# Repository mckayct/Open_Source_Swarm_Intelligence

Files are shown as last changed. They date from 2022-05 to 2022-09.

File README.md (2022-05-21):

# Open Source Swarm Intelligence
<p align="center">
Purpose: Low-Cost Open Source Swarm Capable Robots for Academic Research
</p>
<p align="center">
  
  
   
</p>

## Brief Description:

This repositiory is for the code, paper and files for swarm intelligence research I conducted at Rose-Hulman Institute of Technology under Dr. Michael Wollowski. The end goal of the research was to produce swarm capable robots for academia, that have a wide range of usability at a low-cost. The robots are originally from Kevin Thomas (user tristomietitoredeituit) on Thingiverse [SMARs](https://www.thingiverse.com/thing:2662828), and I modified a housing for them as well as combined some other features.

The final product uses a Mesh Network for communication, and is programmable in Arduino code. I have included all the CAD/STL files, as well as code for people to use. If you use these robots please feel free to share with me what you make! The best way for the swarm intelligence field to grow, is to allow more people to interact with the field.

## Table of Contents

- [Robot Overview](#robot-overview)
- [Photographs of the Robots](#photographs-of-the-robots)
- [Installation](#installation)
- [BOM](#bill-of-materials)
- [Ideas For Future](#ideas-for-future)
- [Credits](#credits)
- [License](#license)
- [Support Me](#support-me)
## Robot Overview

<p align="center">
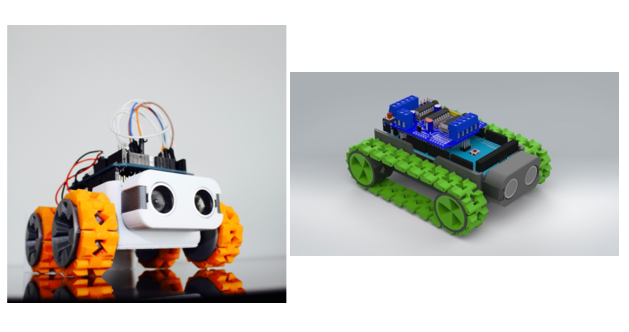
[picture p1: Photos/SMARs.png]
SMARS

</p>

The robotic platform uses a modified 3D printable open source “Screwless/Screwed Modular Assemblable Robotic System” (SMARs) originally designed by Kevin Thomas and modified by Zwald Damien. Kevin Thomas’s page details a plethora of helpful guides as well as his own outline of a teaching schedule for teaching a class with the SMARs robots visualized in Figure 2; however, this course is mainly aimed at high school level students or early undergraduate introductory courses. The SMARs platform is easily produced with a 3D printer and can be modified or expanded upon so long as the creator’s original CC BY-NC-SA 4.0 license is upheld.

<p align="center">
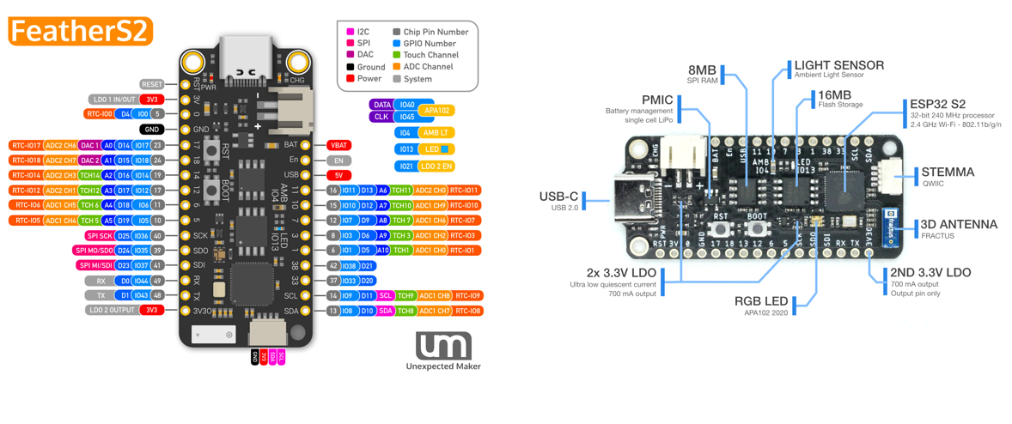
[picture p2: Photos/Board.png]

</p>

For the brain of our robot, we used the FeatherS2 by Unexpected Maker Figure(3). The ESP32-S2 microcontroller was chosen for its ability to be programmed in Arduino code, Circuit Python, or Micro Python and their built-in Wi-Fi communication. This specific ESP32-S2-based board utilizes the Adafruit Feather layout, which allows it to be compatible with Adafruit’s Wing addons. Interchanging Wing modules or stacking them allows new sensors to be added to the robot with ease via a UART connection. 

<p align="center">
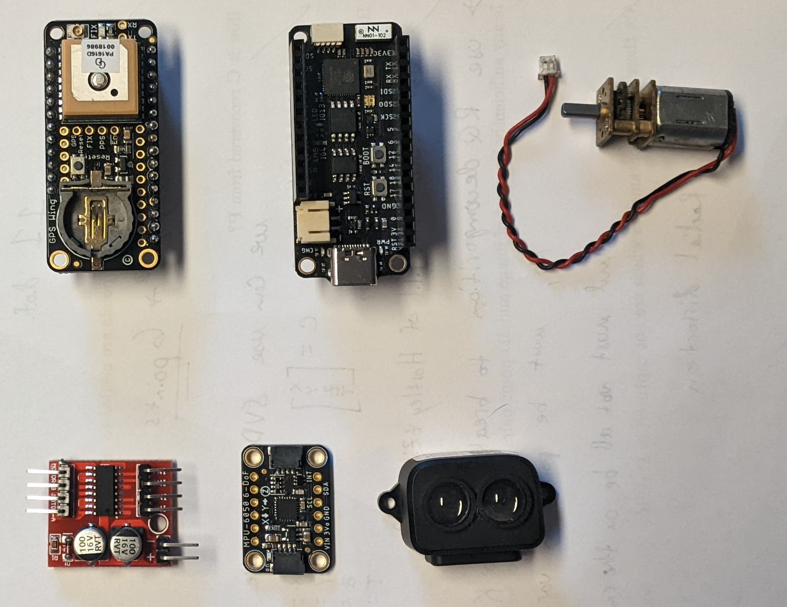
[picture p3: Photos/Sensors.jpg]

</p>
 
In addition, the board has a built-in STEMMA QT connector that allows additional sensors to be connected to the board via I2C connection protocol so long as their I2C addresses are unique. For power, a JST PH LiPo connector allows the use of a 3.7V one-cell LiPo battery which is capable of powering the robot for 6+ hours.  Mobility is provided by a mini dual-channel L298N motor driver, controlling two N20 mini-DC motors with built-in gearboxes. These low-cost motors come in many gear reduction combinations that can allow for faster acceleration or more torque depending on what the buyer is desiring.

## Photographs of the Robots

<p align="center">
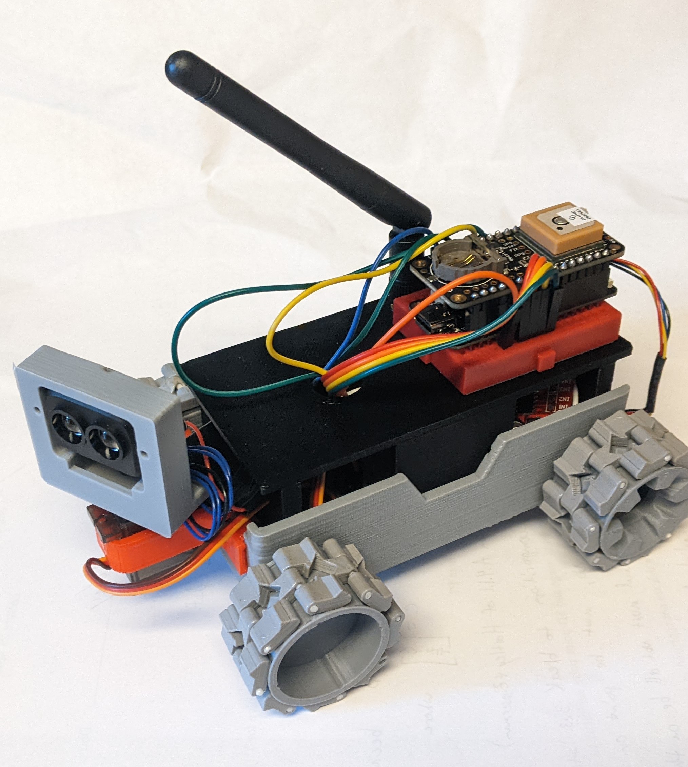
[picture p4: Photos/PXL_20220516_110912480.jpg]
ISO
  
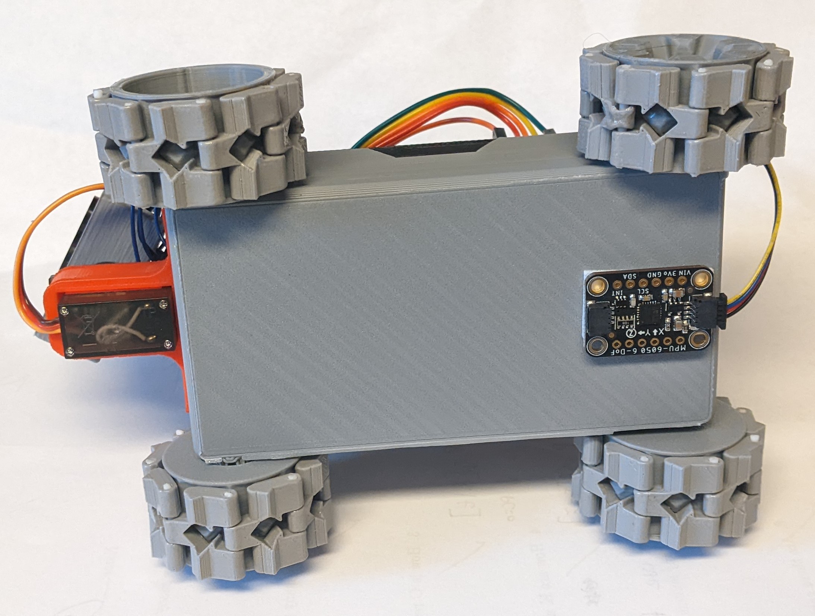
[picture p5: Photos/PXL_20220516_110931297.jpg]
BOTTOM
   
</p>

## Installation

To get the robots working you will need a computer with the Arduino IDE or Circuit Python[^first] setup. The provided code is for Arduino, but these microcontrollers are capable of being coded in either. Users are then encouraged to look through the example code provided, and modify it to their needs.

[^first]: Note at the time of writing, Circuit Python for the ESP32S2 does not support Mesh Networking, so Arduino Coding is preferred right now.

## Bill of Materials

Items are listed below. Users can use links attached or search on other websites for better deals. Sensors can also be changed depending on what the user's end goal is

| Item | Description | Quantity of Component per Robot | Price on Link[^2] | Link  |
| :----: | :---: |  :---: | :---: | :---: |
| Microcontroller | Main control board for Robot | 1 | $24.95 |[Adafruit](https://www.adafruit.com/product/4769) |
| Motor Controller | Controller for N20 Motors | 1 | $13.02 |[Amazon](https://www.amazon.com/Channel-Positive-Inversion-Adjustment-Stepper/dp/B09Y4LKV52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) |
| N20 Motors | N20 Motors with straight gearbox | 2 | $9.49 | [Ebay](https://www.ebay.com/itm/313865598591?hash=item4913d8f67f:g:mnIAAOSwYWFiAJZR)|
| MPU-6050 | 6-D.O.F. Inertial Measuring Unit | 1 | $6.95 | [Adafruit](https://www.adafruit.com/product/3886)|
| Adafruit GPS Featherwing  | Feather Sized GPS Module | 1 | $24.95 |[Adafruit](https://www.adafruit.com/product/3133) |
| TFLuna Point LiDAR | Singular Point LiDAR | 1 | $26.99 |[Amazon](https://www.amazon.com/RCmall-Single-Point-Compatible-Obstacle-Avoidance/dp/B09SZ5H21B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) |
| 9g Servo | 180 Degree Rotational Servo | 1 | $20.99 |[Amazon](https://www.amazon.com/Smraza-Helicopter-Airplane-Control-Arduino/dp/B07L2SF3R4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) |
| LiPo Battery | 2500 mAh Battery | 1 | $14.95 |[Adafruit](https://www.adafruit.com/product/328) |
| Tiny Breadboards | Minature Breadboard for cabling | 2 |  $6.49 |[Amazon](https://www.amazon.com/HiLetgo-SYB-170-Breadboard-Colorful-Plates/dp/B071KCZZ4K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) |
| Dupont Wires | For easy connection between components | 1 | $6.98 | [Amazon](https://www.amazon.com/Elegoo-EL-CP-004-Multicolored-Breadboard-arduino/dp/B01EV70C78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 )|
| 3D printed material | 3D printed components listed in CAD File | 1 | ~$10 | |

[^2]: Does not mean price per robot, nor price per component. Simply price per the link given.

## Ideas for Future

While the current robot was satisfactory for an introduction to Swarm Intelligence, I would eventually like to make them into a more final product including
* Academic Schedule for a Class Based Upon Swarm Intelligence
* Change the drive train to Tank Tread Systems (original SMARs plan)
* Creat New Algorithms for the Swarm
* Look for ways to reduce price

If you create something with this project, please reachout and share it with me!

---
## Credits

### For their Support During my Research
* Dr. Michael Wollowski
  - https://www.rose-hulman.edu/academics/faculty/wollowski-michael-wollowsk.html
  - https://www.rose-hulman.edu/~wollowsk/
* Dr. David Fisher
  - https://www.rose-hulman.edu/academics/faculty/fisher-david-fisherds.html
  - https://wordpress.rose-hulman.edu/fisherds/
* Dr. Carlotta Berry
  - https://www.rose-hulman.edu/academics/faculty/berry-carlotta-berry123.html
  - https://wordpress.rose-hulman.edu/berry123/

### For Tutorials or Foundations to my Research
* Kevin Thomas - SMARs Robot Design
  - https://www.smarsfan.com/
* Unexpected Maker
  - https://feathers2.io/
* Pat Langley
  - https://doi.org/10.1609/aimag.v42i4.15089
* Wikipedia
  - https://en.wikipedia.org/wiki/Swarm_intelligence
* Random Nerd Tutorials
  - https://randomnerdtutorials.com/esp-mesh-esp32-esp8266-painlessmesh/
* Wyss Institute
  - https://wyss.harvard.edu/technology/programmable-robot-swarms/

## License
<p align="center">
<a rel="license" href="http://creativecommons.org/licenses/by-nc-sa/4.0/">
 </a>

<br />
This work is licensed under a <a rel="license" href="http://creativecommons.org/licenses/by-nc-sa/4.0/">Creative Commons Attribution-NonCommercial-ShareAlike 4.0 International License</a>.
</p>

## Support Me
<div align="Center">
 You ABSOLUTELY DO NOT have to, but if you would like to...
 </div>
<p align="center"> 
<a href="https://www.buymeacoffee.com/mckayct" target="_blank">Buy Me A Coffee</a>
 
 </p>
<p align ="center">

</p>

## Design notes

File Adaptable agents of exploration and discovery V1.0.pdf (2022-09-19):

# Adaptable agents of exploration and discovery:

## A swarm robotics platform to facilitate research

### Advisor: Dr. Wollowski Student: Colton McKay

CSSE 435: Swarm Intelligence Dr. Wollowski
Winter/Spring 2021-22

## Abstract

Swarm Intelligence is one of the newest emerging branches of robotics research and has many opportunities for teaching at a collegiate level. As with all research, progress is expedited when more people can engage with the research. In this paper, I will showcase a simple and cheap swarm-capable robot platform. These robots can be used to allow undergraduate students or DIY experts to experiment and explore swarm intelligence. Furthermore, I will showcase an application of these robots to simulate extraterrestrial planetary navigation; an area explored by Pat Langley that I found interesting.

## Introduction

Swarm Intelligence (SI) is the study of the collective behavior of decentralized agents. From these agents, there is a form of self-organization (either natural or artificial) that can be utilized to complete some form of goal. Key aspects of SI swarms are their ability to dynamically grow and decay in population, self-autonomy (no central controlling agent), the ability for each agent within the swarm to sense its abilities and environment, and for the swarm to change goals dynamically (Wikimedia Foundation)

Following these conventions, swarm robots are generally made rather simply to allow mass production such as the Harvard Kilobots as seen in Figure 1. These robots while capable of swarm intelligence, are rather limited in their task completion capabilities. Instead, we created a low-cost robotic platform that is capable of being expanded upon over time to allow professors and students to adapt the robots to their current research goals. This modularity allows professors to utilize these robots within a classroom setting on a budget, create new course plans, or allow students to change the robots to their common goal.

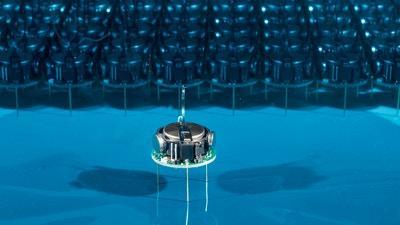
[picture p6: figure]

Figure 1: Wyss Institute at Harvard University

## The Robotic Platform

The robotic platform uses a modified 3D printable open source “Screwless/Screwed Modular Assemblable Robotic System” (SMARs) originally designed by Kevin Thomas and modified by Zwald Damien. Kevin Thomas’s page details a plethora of helpful guides as well as his own outline of a teaching schedule for teaching a class with the SMARs robots visualized in Figure 2; however, this course is mainly aimed at high school level students or early undergraduate introductory courses. The SMARs platform is easily produced with a 3D printer and can be modified or expanded upon so long as the creator’s original CC BY-NC-SA 4.0 license is upheld.

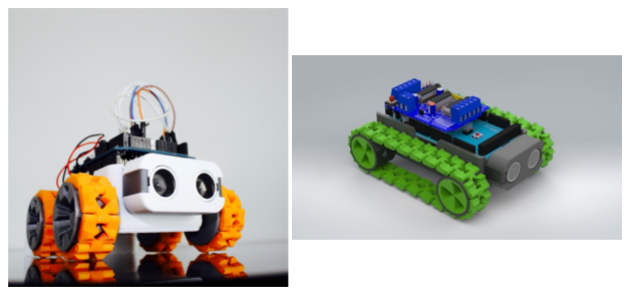
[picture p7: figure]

Figure 2: SMARS robotic platform by Kevin Thomas (left) and a remixed design by Zwald Damien (right)

For the brain of our robot, we used the FeatherS2 by Unexpected Maker Figure(3). The ESP32-S2 microcontroller was chosen for its ability to be programmed in Arduino code, Circuit Python, or Micro Python and its built-in Wi-Fi communication. This specific ESP32-S2-based board utilizes the Adafruit Feather layout, which allows it to be compatible with Adafruit’s Wing addons. Interchanging Wing modules or stacking them allows new sensors to be added to the robot with ease via a UART connection.

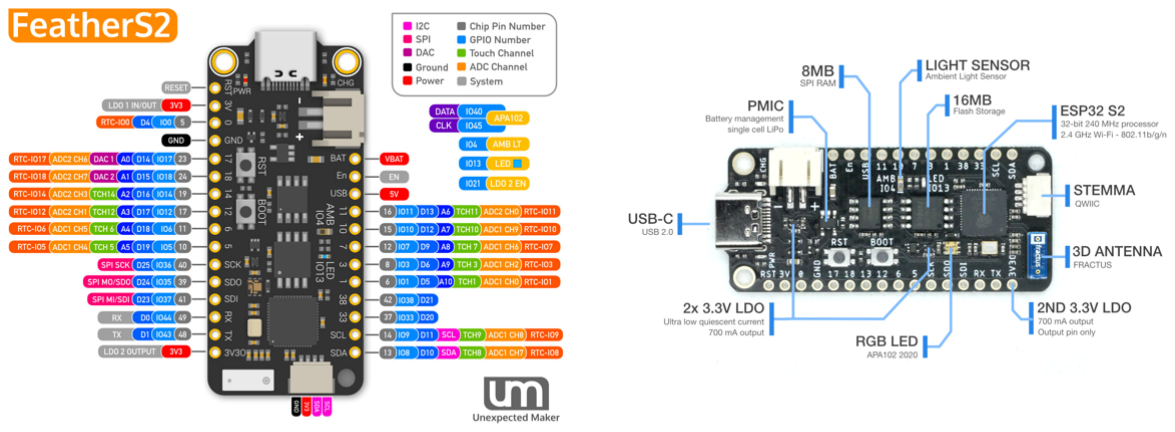
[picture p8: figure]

Figure 3: FeatherS2 features and pinout diagrams by Unexpected Maker

In addition, the board has a built-in STEMMA QT connector that allows additional sensors to be connected to the board via I2C connection protocol so long as their I2C addresses are unique. For power, a JST PH LiPo connector allows the use of a 3.7V one-cell LiPo battery which is capable of powering the robot for 6+ hours. Mobility is provided by a mini dual-channel L298N motor driver, controlling two N20 mini-DC motors with built-in gearboxes. These low-cost motors come in many gear reduction combinations that can allow for faster acceleration or more torque depending on what the buyer is desiring.

## Pat Langley’s Agents of Exploration and Discovery

Pat Langley from the Institute for Defense Analyses authored an amazing paper on the use of artificial intelligence-powered robots or “agents of exploration and discovery” to perform as modern-day pioneers that can explore new novel environments and construct maps, perform scientific experiments, and prepare for future exploration by humankind. Langley goes on further to state that these agents must be capable of autonomous behaviors, capable of variable locomotion, and able to have a variety of sensors attached to them. While the scope of our paper does not allow for professional-level robotics akin to a swarm of NASA’s JPL rovers, we can utilize the robotic platform we have made to further research

Langley suggests for these robots to be able to explore they should be able to perform Localization, Target Selection, Navigation, and Mapping. Our current system detailed above could perform a rudimentary form of Simultaneous Localization and Mapping (SLAM) via sensor fusion of the IMU, GPS, and LiDAR data. Once SLAM is performed, obstacle avoidance using LiDAR in conjunction with the map created would allow the robot to successfully navigate to areas of interest. Finally, target selection can be performed as part of the swarm’s algorithm, for example searching for a point of lowest elevation on an extraterrestrial planet as it may have extant evidence of life or exploring the highest peaks as they may contain frozen water.

While the current robots described above lack discovery capabilities, this can be expanded by adding more sensors to the system. The key points the robots should be able to perform are taxonomy formation, Descriptive law induction, and explanatory model construction. Taxonomy formation is the process of making scientific discoveries and mapping them into classes and subclasses via characteristics; therefore, providing an identification nomenclature to them. Descriptive law induction refers to taking the classes and subclasses formed within taxonomy and applying qualitative relationships or numerical equations to describe how classes and subclasses interact with each other. Once these relationships are constructed you can form the explanatory models for these discoveries. Models such as these would allow for hypotheses to be formulated, laws created, and observations documented. A picture relating all of these processes together can be seen below in Figure(2) provided by Langley.

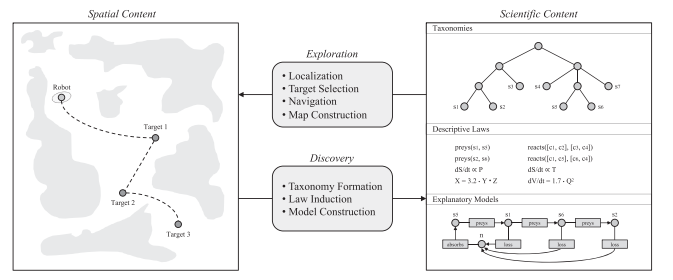
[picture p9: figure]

Figure 4: How exploration and discovery inform the complementary process of gathering spatial and scientific data

## Wollowski and McKay’s Agents of Exploration and Discovery

Using the above basis, Dr. Wollowski and I have proposed a novel example of how future research and approach agents of exploration and discovery, by harnessing the power of swarm intelligence and cheap but adaptable robotics. Our algorithm utilizes the ESP32S2’s Mesh creation tool, as well as a particle swarm optimization (PSO) approach. Our goal is for the robots to explore a foreign terrain, searching for areas of interest, in our case areas of low elevation. The data from the robots is shared by the Mesh network to allow global variable cohesion between agents in the swarm. A separate observing ESP32S2 on the network acts as our “satellite” for the agents and allows us to view the data each robot is collecting while not interfering with or controlling any of the respective agents.

## The Code

Our code written in Arduino is available on GitHub. The code uses the Painless Mesh by author Coopdis, Scotty et al. as a basis. This Mesh network is the foundation that allows our swarm to be dynamic in nature while also allowing each agent to share information globally. The network allows for each agent in the swarm to function as its own master, providing the autonomy Langley desired. A visual example of a simple network can be seen in Figure(1). Localization for the robots is provided by the onboard GPS system, which can provide accurate location data within two meters by using a universal transverse Mercator conversion from a geographic coordinate system. Our target is pre-selected, and navigation is performed by using our GPS, and LiDAR to avoid obstacles. Maps of the environment are created from LiDAR, IMU, and GPS data.

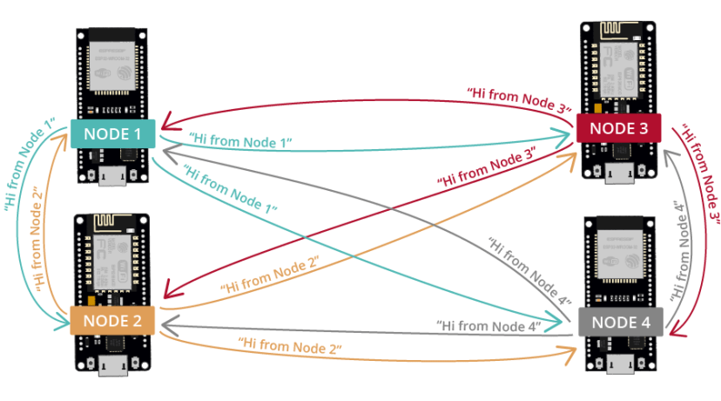
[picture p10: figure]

Figure 5: Visualization of a Mesh Network by randomnerdturotials.com

Task scheduler, an Arduino library created by Anatoli Arkhipenko is in our mesh to prevent any

one agent from controlling the network or allowing the network to fall apart. The task scheduler also schedules our robots to autonomously run functions with preset time schedules.

## The Code

The current rendition of the code is available for free at my GitHub repository, as well as plans for the robots and supporting material.

## Conclusion and Future

The following approach is easily adaptable to a university-level course on swarm intelligence. The robotics platform while cheap is very modular and can be changed to suit a novel pursuit of agents of exploration and discovery. We have included in the appendix of this paper, a rough outline of topics a typical semester-based college course could follow to teach students about swarm intelligence. Furthermore, our code, schematics, and experimentation are outlined in detail and are open source. Our experiment using a particle swarm optimization algorithm on the robotic platform was a failure as with the current code we were unable to fully implement the algorithm. In hindsight, future researchers wishing to apply the same algorithm could work to improve upon this experiment by taking the robots and building them to accommodate their own goals and procedures.

## References

1. “Introducing the feathers2!” FeatherS2, https://feathers2.io/.
2. Langley, Pat. “Agents of Exploration and Discovery.” AI Magazine, vol. 42, no. 4, 2022, pp. 72–82.,

https://doi.org/10.1609/aimag.v42i4.15089.

3. “Programmable Robot Swarms.” Wyss Institute, 28 May 2021,

https://wyss.harvard.edu/technology/programmable-robot-swarms/.

4. Strobistar, et al. “ESP-Mesh with ESP32 and ESP8266: Getting Started.” Random Nerd Tutorials, 23 Nov.

2020, https://randomnerdtutorials.com/esp-mesh-esp32-esp8266-painlessmesh/.

5. “Swarm Intelligence.” Wikipedia, Wikimedia Foundation, 26 Apr. 2022,

https://en.wikipedia.org/wiki/Swarm_intelligence.

6. “Welcome to SMARS Fan.” RSS, https://www.smarsfan.com/.

## Appendix

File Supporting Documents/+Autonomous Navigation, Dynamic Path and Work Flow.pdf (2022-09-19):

ABSTRACT

Kennedy Space Center has teamed up with the Biological Computation Lab at the University of New Mexico to create a swarm of small, low-cost, autonomous robots, called Swarmies, to be used as a ground-based research platform for in-situ resource utilization missions. The behavior of the robot swarm mimics the central-place foraging strategy of ants to find and collect resources in an unknown environment and return those resources to a central site. The swarm has no prior knowledge of the environment, uses trails as a simple indirect communication strategy, and evolves a set of behavioral parameters using a genetic algorithm. The evolution of the parameters allows the swarm to maximize collection rates while adapting to new environmental conditions and to various unknown resource distributions. The goal of this research is to add new in-situ resource utilization related behaviors to the genetic algorithm and to increase the autonomy of the system.

ANTICIPATED BENEFITS
To NASA funded missions:
This research area provides several possible benefits to NASA’s Science Technology Mission Directorate (STMD) Game Changing Development (GCD) Human Robotic System (HRS) projects such as Regolith Advanced Surface Systems Operations Robot (RASSOR) 2 which is under development at KSC’s Swamp Works. Off-planet applications of such a system include water-ice detection and mining, terrain mapping and habitat construction in advance of human explorers. The confirmation of the viable concept of operations along with the proof of concepts for autonomous navigation, path planning, and power management could improve performance and reliability of in-situ robotic mining agents such as RASSOR2. The

Two Swarmie robots are shown here searching for resources, or bar codes. NASA photo.

Table of Contents
Abstract
Anticipated Benefits
Technology Maturity
Management Team
Technology Areas
Detailed Description
U.S. Locations Working on this Project
Image Gallery
Details for Technology 1
Details for Technology 2
Details for Technology 3

Completed Project (2014 - 2015)

## Autonomous Navigation, Dynamic Path and Work Flow Planning in Multi-Agent Robotic Swarms Project

Center Innovation Fund: KSC CIF Program | Space Technology Mission
Directorate (STMD)

For more information visit techport.nasa.gov

Some NASA technology projects are smaller (for example SBIR/STTR, NIAC and Center Innovation Fund), and will have less content than other, larger projects. Newly created projects
may not yet have detailed project information. | Printed 7/24/2015

Page 1

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
10 development environment, including the simulation verification environment, along with the low cost robotic platforms reduce the cost of design and development of software for these types of applications.
To NASA unfunded & planned missions:
This research provides potential benefit to any unfunded & planned NASA missions such as OxMiner or an Asteroid Retrieval Mission engaged in in-situ resource mining. Off-planet applications of such a system include water-ice detection and mining, terrain mapping and habitat construction in advance of human explorers. The confirmation of the viable concept of operations along with the proof of concepts for the autonomous navigation, path planning, and power management improves performance and reliability of in-situ robotic mining agents.The development environment, including the simulation verification environment, along with the low cost robotic platforms reduce the cost of design and development of software for these types of applications.
To other government agencies:
This research provides potential benefit to other government agencies such as the Department of Defense (DOD) or Defense Advanced Research Projects Agency (DARPA) engaged in in-situ resource location and operations. Terrestrial applications include search-and-rescue, hazardous waste cleanup, land mine removal and infrastructure inspection and repair. The approach used in the software could also be adapted to search the Internet or to search large unknown data sets. The confirmation of the viable concept of operations along with the proof of concepts for the autonomous navigation, path planning, and power management improves performance and reliability of in-situ robotic operations. The development environment, including the simulation verification environment, along with the
Lowest: 2 | | Highest: 3
1 | 2 | | 3 | 4 | 5 | 6 | 7 | 8 | 9
Applied Research | | | | Develop- ment | | | Demo & Test

Technology Maturity

Management Team
Program Executive:
John Falker

Program Manager:
Nancy Zeitlin

Project Manager:
Kurt Leucht

Principal Investigator:
Kurt Leucht

Co-Investigator:
Karl Stolleis

Technology Areas
Robotics, Tele-Robotics &
Autonomous Systems (TA 4)

## Autonomous Navigation, Dynamic Path and Work Flow Planning in Multi-Agent Robotic Swarms Project

Center Innovation Fund: KSC CIF Program | Space Technology Mission
Directorate (STMD)

For more information visit techport.nasa.gov

Some NASA technology projects are smaller (for example SBIR/STTR, NIAC and Center

Page 2 low cost robotic platforms reduce the cost of design and development of software for these types of applications.
To the commercial space industry:
This research provides potential benefit to the commercial space industry commercial asteroid mining ventures which are proposed by Planetary Resources, Inc., Deep Space Industries, Inc. Moon Express, Astrobotics, or any entity engaged in in-situ resource location and operations. Off-planet applications of such a system include water-ice detection and mining, terrain mapping and habitat construction in advance of human explorers. The confirmation of the viable concept of operations along with the proof of concepts for the autonomous navigation, path planning, and power management improves performance and reliability of in-situ robotic operations. The development environment, including the simulation verification environment, along with the low cost robotic platforms reduce the cost of design and development of software for these types of applications.
To the nation:
Terrestrial applications include search-and-rescue, hazardous waste cleanup, land mine removal and infrastructure inspection and repair. The approach used in the software could also be adapted to search the Internet or to search large unknown data sets. The development environment, including the simulation verification environment, along with the low cost robotic platforms reduce the cost of design and development of software for these types of applications.These technologies could make these terrestrial operations safer and more efficient via swarming robotic means.

DETAILED DESCRIPTION

As humans push further beyond the grasp of earth, robotic missions in advance of human missions will play an increasingly important role. These robotic systems will find and collect valuable resources as part of an in-situ resource utilization strategy. They will need to be highly autonomous while maintaining high task performance levels.
Kennedy Space Center has teamed up with the Biological Computation Lab at the University of New Mexico to create a swarm of small, low-cost, autonomous robots, called Swarmies, to be used as a ground-based research platform for in-situ resource utilization missions. The behavior of the robot swarm mimics the central-place foraging strategy of ants to find and collect resources in an unknown environment and return those resources to a central site. The swarm has no prior

## Autonomous Navigation, Dynamic Path and Work Flow Planning in Multi-Agent Robotic Swarms Project

Center Innovation Fund: KSC CIF Program | Space Technology Mission
Directorate (STMD)

For more information visit techport.nasa.gov

Some NASA technology projects are smaller (for example SBIR/STTR, NIAC and Center

Page 3 knowledge of the environment, uses trails as a simple indirect communication strategy, and evolves a set of behavioral parameters using a genetic algorithm. The evolution of the parameters allows the swarm to maximize collection rates while adapting to new environmental conditions and to various unknown resource distributions.
The goal of this research is to add new in-situ resource utilization related behaviors to the genetic algorithm and to increase the autonomy of the system. Digital trails that are based on ant pheromone trails provide simple communication of resource locations between robots but they also provide some assistance with obstacle avoidance and navigation. Two newly evolved genetic algorithm parameters allow the robots to recharge their batteries autonomously without loss of robots due to insufficient charge. The genetic algorithm is able to optimize collection rates while also dealing with relatively high system error due to inexpensive and sub-optimal sensors onboard the robots. The distributed nature of the robotic swarm prevents a single point of failure and allows the system to operate even with the loss of one or more robots.
Off-planet applications of such a system include water-ice detection and mining, terrain mapping and habitat construction in advance of human explorers. Terrestrial applications include searchand-rescue, hazardous waste cleanup, land mine removal and infrastructure inspection and repair. The approach used in the software could also be adapted to search the Internet or to search large unknown data sets.
This project has helped demonstrate that in an obstacle laden environment, trails used as a simple indirect communication strategy can allow a swarm of small, low-cost robots to collect resources in an optimal manner when coupled with a genetic algorithm to evolve behaviors. This project has also helped demonstrate that an autonomous robot swarm can evolve battery charging behavior using a genetic algorithm to minimize or eliminate dead robots due to insufficient charge.
The project has been successful in meeting the original goals in simulated field trials and also in real robots. The genetic algorithm is able to evolve optimal behaviors allowing for efficient resource collection while coping with various obstacle arrangements and resource distributions. The genetic algorithm is also able to maintain a high level of fitness while incorporating autonomous recharging of the robots. It has also been demonstrated that this system is error tolerant, adaptable to different robot types, and is scalable in both environment size and numbers of robots.
All of these robot behaviors are performed in real-time with a small, low-cost onboard computer and small memory footprint. The robot platform is constructed using commercial off-the-shelf parts and

## Autonomous Navigation, Dynamic Path and Work Flow Planning in Multi-Agent Robotic Swarms Project

Center Innovation Fund: KSC CIF Program | Space Technology Mission
Directorate (STMD)

For more information visit techport.nasa.gov

Some NASA technology projects are smaller (for example SBIR/STTR, NIAC and Center

Page 4

3D printed parts with a total cost of less than $1,500 per robot.
A secondary goal of this project was to extend the genetic algorithm to other new and commercially available robot platforms. Another secondary goal was to use open source software frameworks to help reduce barriers and allow future researchers to more easily utilize genetic algorithms for behavior evolution in a swarm of robots. The project has been successful in meeting both of these secondary goals.
This autonomous mobile robot system is a foundation for future research into the suitability of robot swarms and evolutionary algorithms for in-situ resource utilization missions. The low-cost of this type of system removes one of the barriers typically associated with swarm operation and research. Such research should prove valuable as humans explore harsh, remote, or inaccessible locations where teleoperation is required.

## Autonomous Navigation, Dynamic Path and Work Flow Planning in Multi-Agent Robotic Swarms Project

Center Innovation Fund: KSC CIF Program | Space Technology Mission
Directorate (STMD)

For more information visit techport.nasa.gov

Some NASA technology projects are smaller (for example SBIR/STTR, NIAC and Center

Page 5

## Autonomous Navigation, Dynamic Path and Work Flow Planning in Multi-Agent Robotic Swarms Project

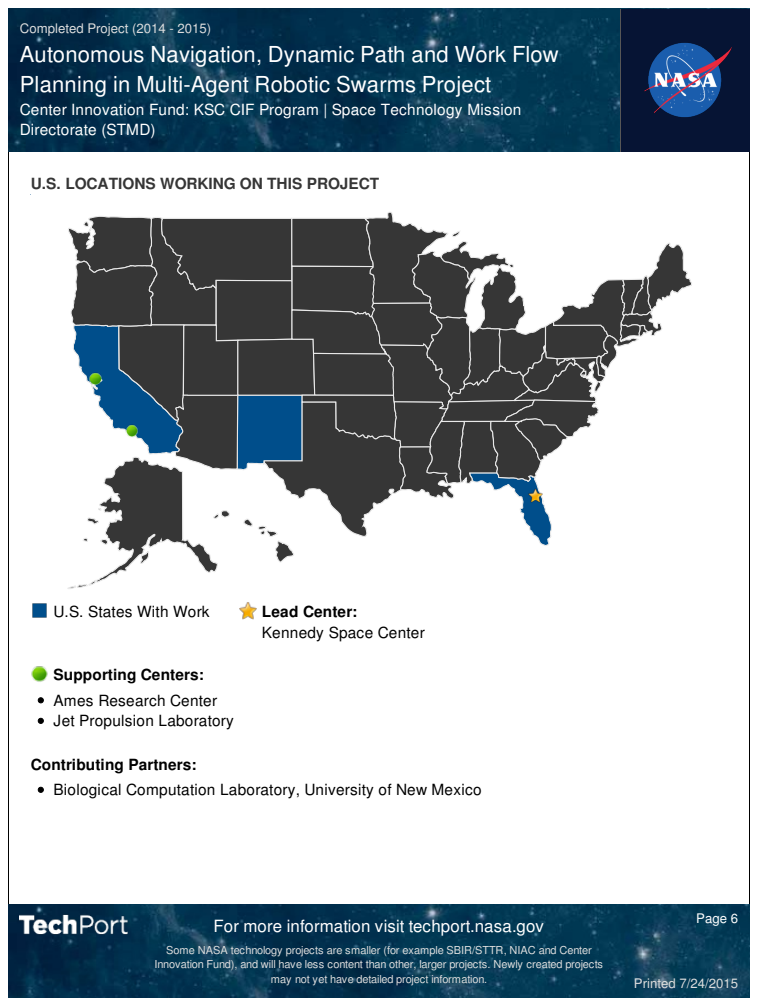
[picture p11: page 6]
U.S. States With Work; Lead Center:; Page 6

Center Innovation Fund: KSC CIF Program | Space Technology Mission
Directorate (STMD)

U.S. LOCATIONS WORKING ON THIS PROJECT

Kennedy Space Center

Supporting Centers:
Ames Research Center
Jet Propulsion Laboratory

Contributing Partners:
Biological Computation Laboratory, University of New Mexico

For more information visit techport.nasa.gov

Some NASA technology projects are smaller (for example SBIR/STTR, NIAC and Center

PROJECT LIBRARY
News Stories
Discovery News: Swarmie Space Robots Forage Like Ants (http://news.discovery.com/tech/robotics/swarmie-space-robots-forage-like-ants-140821.htm)
Engadget: NASA's Swarmies are a squad of smaller, less intelligent rovers (http://www.engadget.com/2014/08/27/nasa-swarmies/)
Fast Company: These Robots Will Mine Outer Space For Water And Minerals (http://www.fastcoexist.com/3034904/these-robots-will-mine-outer-space-for-water-andminerals)
IEEE Spectrum: NASA Training Swarmie Robots for Space Mining (http://spectrum.ieee.org/automaton/robotics/military-robots/nasa-training-swarmie-robotsfor-space-mining)
NASA Kennedy YouTube video: Inside KSC! Feb 27, 2015 (https://www.youtube.com/watch?v=mYlBabMIesE)
NASA Kennedy YouTube video: Swarmies Work Through Field Tests (https://www.youtube.com/watch?v=kjSD6DWk0OM)
NASA Website: Meet The Swarmies - Robotics Answer to Bugs (http://www.nasa.gov/content/meet-the-swarmies-robotics-answer-to-bugs/) NASA Website: Swarmies Shuffle Through Field Tests (http://www.nasa.gov/content/swarmies-shuffle-through-field-tests/)
SPACE.com: NASA's Robot Army of Swarmies Could Explore Other Planets (http://www.space.com/26935-nasa-robot-swarmies-army-space-exploration.html) Spaceport Magazine (cover story): Robots Take World by Swarm (http://issuu.com/spaceportmagazine/docs/september_spm)
Spaceport Magazine: Engineers seek more efficient search from Swarmies Continued on following page.

## Autonomous Navigation, Dynamic Path and Work Flow Planning in Multi-Agent Robotic Swarms Project

Center Innovation Fund: KSC CIF Program | Space Technology Mission
Directorate (STMD)

For more information visit techport.nasa.gov

Some NASA technology projects are smaller (for example SBIR/STTR, NIAC and Center

Page 7

News Stories (cont.)
(http://issuu.com/spaceportmagazine/docs/spaceport_magazine_____march_2015) WOFL FOX 35 Orlando (video segment): NASA programming robots to act like ants (http://www.myfoxorlando.com/story/26427492/nasa-programming-robots-to-act-like-ants)

This image shows a computer simulation of a swarm of robots searching for resources, or bar codes, among a field of obstacles. The inlay shows a map containing obstacles in white and found resources in black.

This image shows a swarm of four robots searching for resources, or bar codes, in a NASA parking lot.

IMAGE GALLERY

DETAILS FOR TECHNOLOGY 1

Technology Title
Autonomy
Technology Description
This technology is categorized as complex electronics software for ground support or mission operations
see detailed description
Capabilities Provided
see detailed description

Technology Areas
Other Technology Areas:
Robotics, Tele-Robotics &
Autonomous Systems (TA 4)

## Autonomous Navigation, Dynamic Path and Work Flow Planning in Multi-Agent Robotic Swarms Project

Center Innovation Fund: KSC CIF Program | Space Technology Mission
Directorate (STMD)

For more information visit techport.nasa.gov

Some NASA technology projects are smaller (for example SBIR/STTR, NIAC and Center

Page 8

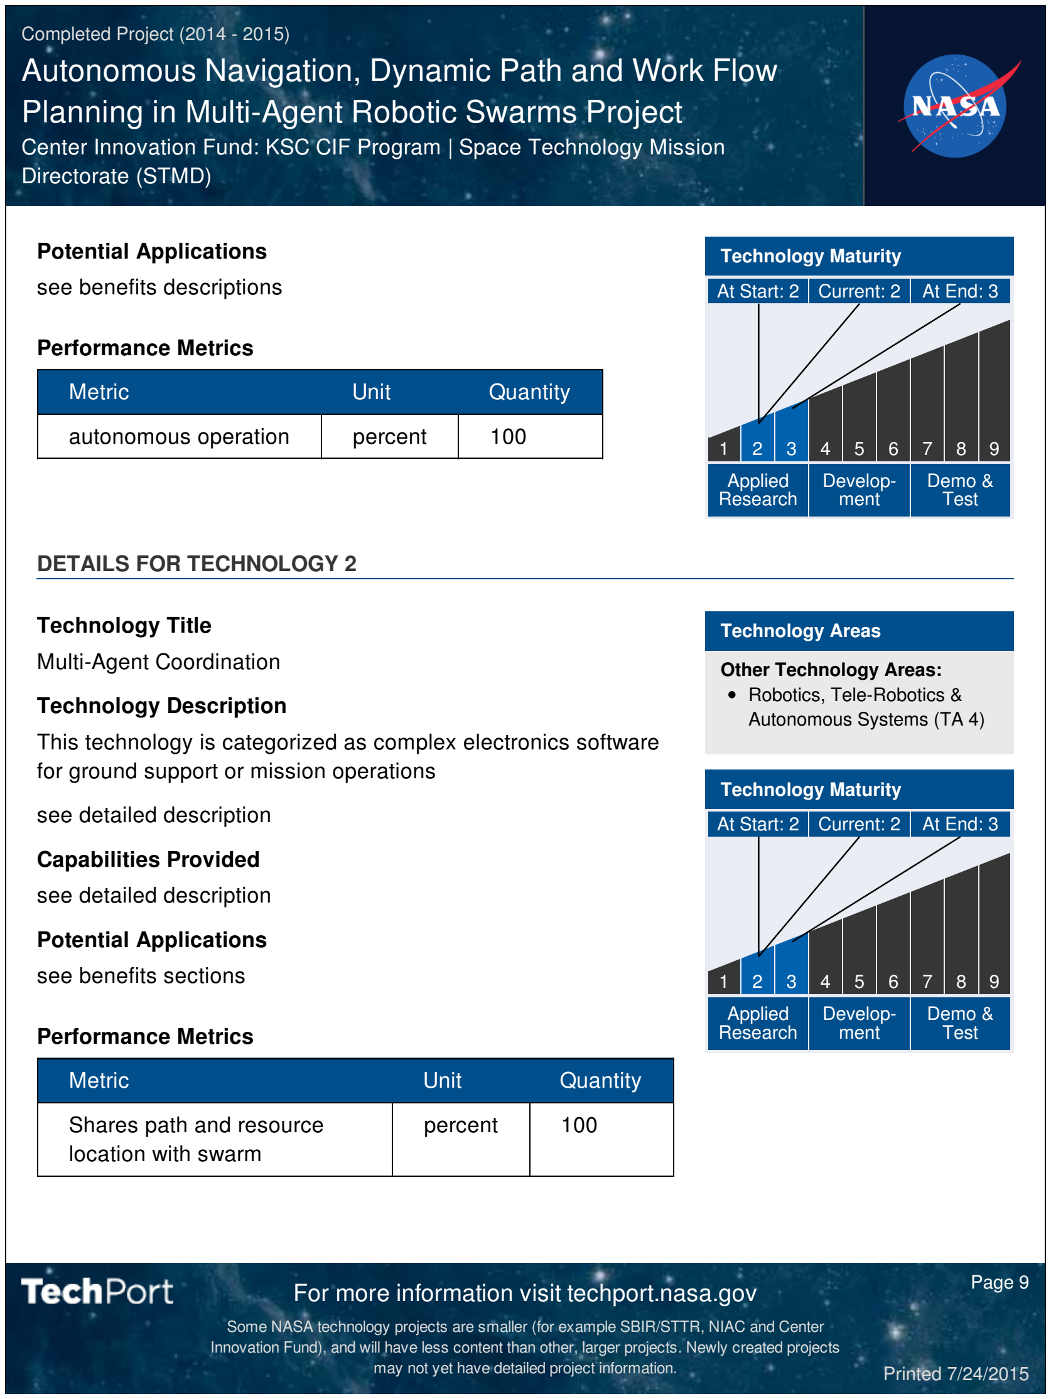
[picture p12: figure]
Potential Applications see benefits descriptions; Performance Metrics; Metric; Unit; Quantity; autonomous operation; percent; At Start: 2; Current: 2; At End: 3; Applied Research; Develop- ment; Demo & Test; Technology Maturity; DETAILS FOR TECHNOLOGY 2; Technology Title Multi-Agent Coordination; Technology Description; see detailed description; Capabilities Provided see detailed description; Potential Applications see benefits sections; Shares path and resource location with swarm; Technology Areas; Other Technology Areas: Robotics, Tele-Robotics & Autonomous Systems (TA 4)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

This technology is categorized as complex electronics software for ground support or mission operations

## Autonomous Navigation, Dynamic Path and Work Flow Planning in Multi-Agent Robotic Swarms Project

Center Innovation Fund: KSC CIF Program | Space Technology Mission

Some NASA technology projects are smaller (for example SBIR/STTR, NIAC and Center

DETAILS FOR TECHNOLOGY 3

Technology Title
Path and Motion Planning with Uncertainty
Technology Description
This technology is categorized as complex electronics software for ground support or mission operations
see details description
Capabilities Provided
see details description
Potential Applications
see benefits section

Performance Metrics
Metric | Unit | Quantity
navigates successfully to resource | percent | 100
At Start: 2 | Current: 2 | At End: 3

Applied
Research

Develop- ment

Demo &
Test

Technology Areas
Other Technology Areas:
Robotics, Tele-Robotics &
Autonomous Systems (TA 4)

Technology Maturity

## Autonomous Navigation, Dynamic Path and Work Flow Planning in Multi-Agent Robotic Swarms Project

Center Innovation Fund: KSC CIF Program | Space Technology Mission
Directorate (STMD)
1 | 2 | 3 | 4 | 5 | 6 | 7 | 8 | 9

For more information visit techport.nasa.gov

Some NASA technology projects are smaller (for example SBIR/STTR, NIAC and Center

Page 10

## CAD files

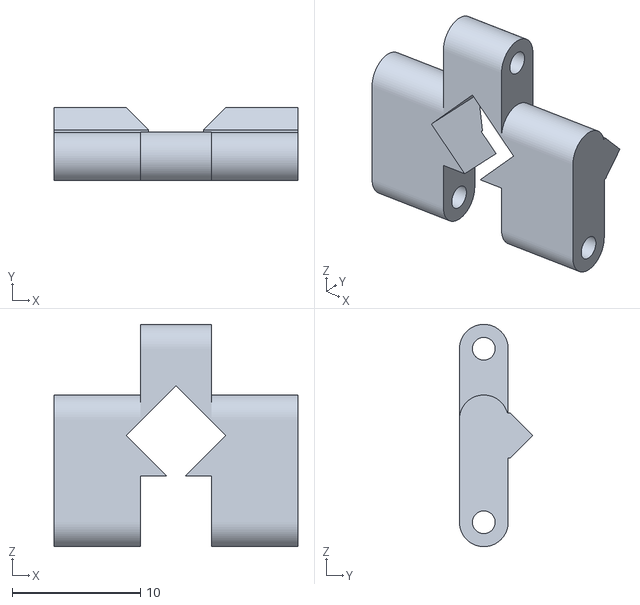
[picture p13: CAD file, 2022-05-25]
CAD/SMARS-Chain.STL
19.0 x 5.70 x 17.3

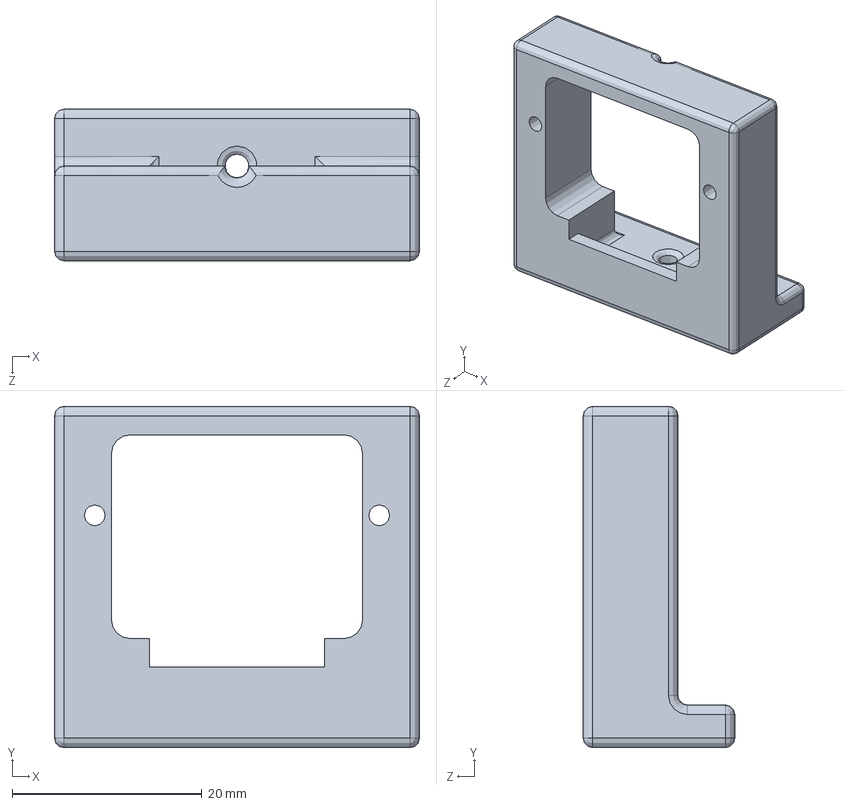
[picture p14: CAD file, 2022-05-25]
CAD/LiDAR Holder.SLDPRT
38.5 x 36.0 x 16.0 mm

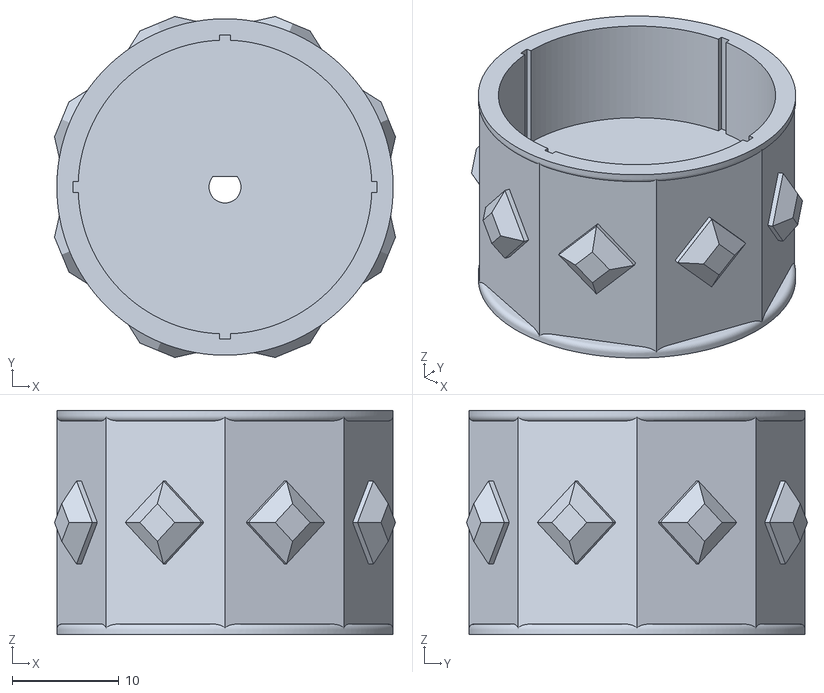
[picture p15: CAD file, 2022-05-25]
CAD/SMARS-Drive-Wheel.STL
31.9 x 31.9 x 21.0

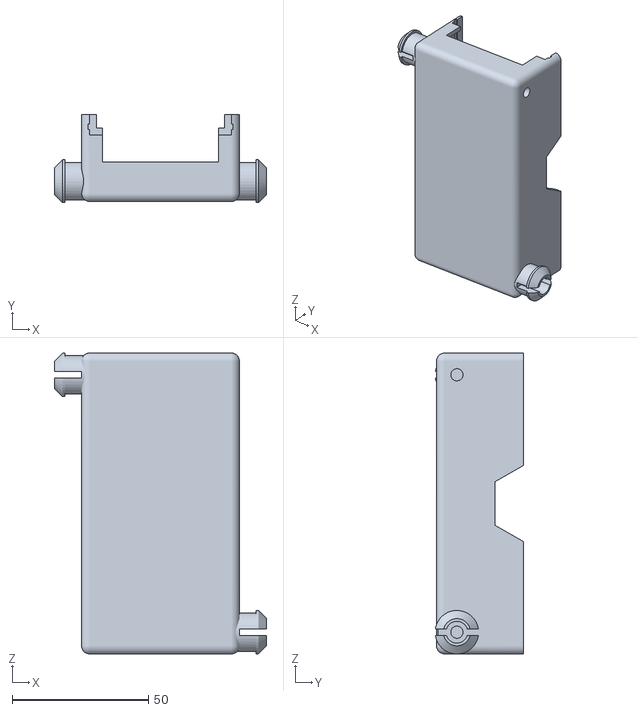
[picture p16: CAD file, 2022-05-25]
CAD/SMARS-Chassis-L-No-Middle-Partition.stl
78.0 x 32.4 x 110.5

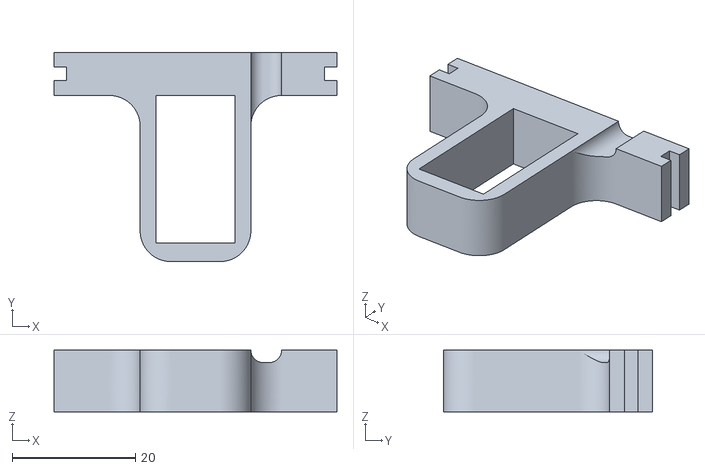
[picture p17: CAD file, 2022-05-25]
CAD/Servo-Holder.stl
46.0 x 34.0 x 10.0

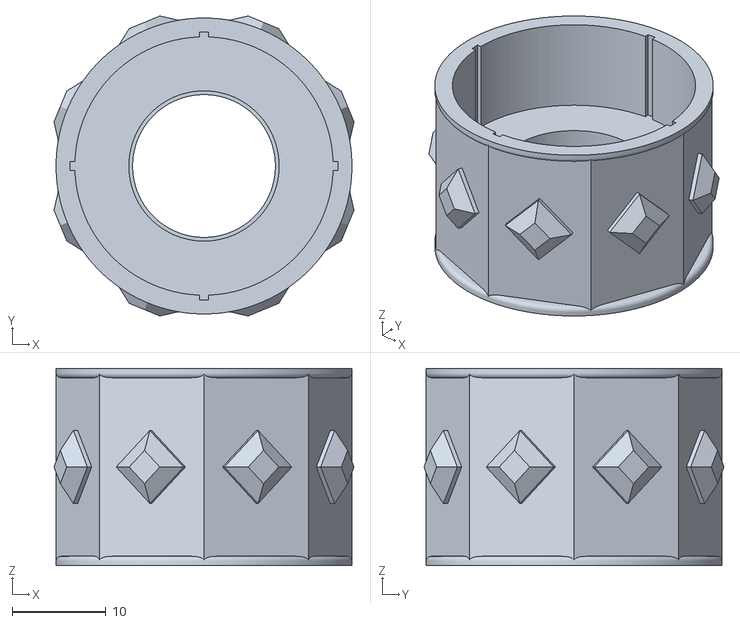
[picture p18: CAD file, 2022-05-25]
CAD/SMARS-Passive-Wheel.STL
31.9 x 31.9 x 21.0

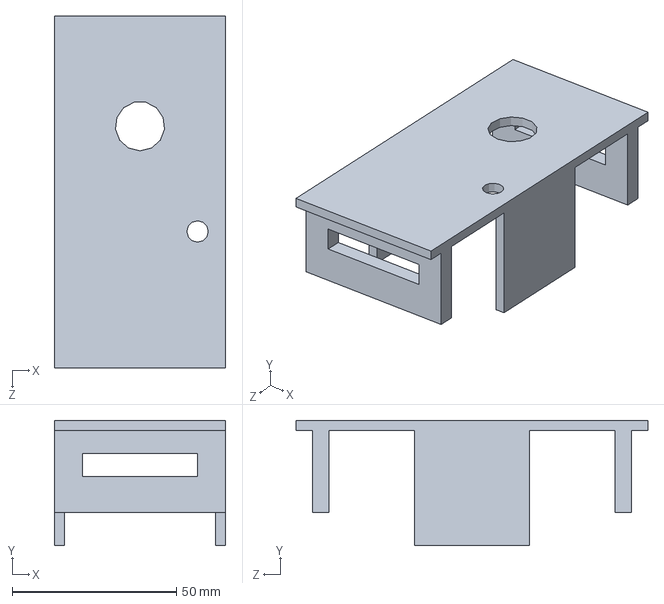
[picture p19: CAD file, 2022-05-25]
CAD/Faceplate.SLDPRT
52.0 x 38.0 x 107.0 mm

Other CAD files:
CAD/Faceplate.STL
CAD/LiDAR Holder.STL

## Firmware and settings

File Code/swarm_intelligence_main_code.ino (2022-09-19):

 /* Swarm Intelligence Code
  Rose-Hulman Institute of Technology
  Winter-Spring 2021-22

  By: Colton McKay
      school email: mckayct@rose-hulman.edu
      personal email: wcsm1999@yahoo.com

  Advisor: Dr. Wollowski

  Description:
  This code is the main driving code for my swarm robots (for more information on them see README).
  The code uses a painlessMesh Library to form a WIFI network using ESP-MESH protocals, this allows for dynamic network decay and growth
  The code also includes our algorithm for what the Robots must accomplish as well as some defined movement functions.
  My coding style is not "Rose-Hulman" standard, but I organize it into logical chunks for easier understanding. If future students need any help
  or would like to understand my work flow/process feel free to reach out to me via contact info above.

*/

// Import of Libraries
#include <basicMPU6050.h> 
#include <Adafruit_GPS.h>
#include <Adafruit_Sensor.h>
#include <Wire.h>
#include <Arduino.h>     // every sketch needs this
#include <TFLI2C.h>      // TFLuna-I2C Library v.0.2.0
#include <L298NX2.h>
#include "painlessMesh.h" //Used for making the WIFI Mesh Network


//**********************************************************
// #Defines go here

#define GPSSerial Serial1 // Define GPS Serial Connection
#define   MESH_PREFIX     "swarmIntelligence" // WIFI Network Name
#define   MESH_PASSWORD   "swarmsRCool" // WIFI Network Password
#define   MESH_PORT       5555 // TCP Port Network runs on, 5555 is default
#define GPSECHO false //Set to true to print Raw GPS Data to Serial. For Debugging only!
//  Pin definition
//Motor A Pins
const unsigned int EN_A = 3;
const unsigned int IN1_A = 5;
const unsigned int IN2_A = 6;
//Motor B Pins
const unsigned int IN1_B = 7;
const unsigned int IN2_B = 8;
const unsigned int EN_B = 9;
//Constants for Measuring Motion Time
unsigned long startMillis;  //some global variables available anywhere in the program
unsigned long currentMillis;
const unsigned long period = 1000;  //the value is a number of milliseconds (1 second), scale as needed
const unsigned long timeConstInches = 10; // Constant variable in milliseconds that translate to roughly 1 inch of motion
const unsigned long timeConstDegree = 10; // Constant variable in milliseconds that translate to roughly 1deg of rotation motion
//Constants for LIDAR
int16_t tfDist;    // distance in inches (sensor reads in cm, I have converted)
int16_t  tfAddr = TFL_DEF_ADR;  // use this default I2C address or
//Servo for LIDAR
const int servoPin = 17;
int dutyCycle = 0;
const int PWMFreq = 50;                                //50hz
const int PWMChannel = 0;
const int PWMResolution = 12;                       //12 bits 0-4095

//***********************************************************************
// Declare Class objects Here

Scheduler userScheduler; // to control your personal task
painlessMesh  mesh; //Create a mesh
L298NX2 motors(EN_A, IN1_A, IN2_A, EN_B, IN1_B, IN2_B);// Initialize both motors
Adafruit_GPS GPS(&GPSSerial);//Define GPS Object
TFLI2C tflI2C;
basicMPU6050<> imu;


//**********************************************************************
// Declare Global Variables Here

void sendMessage() ; // Prototype so PlatformIO doesn't complain
//void updateLocalVariables();
//void updateGlobalVariables();
//void algorithm();
//void readData();
//void obstacleAvoidance();
////void gatherData();
//void randomStart();
//void movements();
//**********************************************************************
// Declare Tasks for Task Manager Here
//(WHEN, HOW OFTEN, TASK)
Task taskSendMessage( TASK_SECOND*1 ,1000, &sendMessage ); // Used to Ping to Network, Data

//Task taskRandomStart( -1 ,0, &randomStart);
//
//Task tastkUpdateGlobalVariables(-1, 0, &updateGlobalVariables );//Used to check and update Global Variables
//
//Task taskUpdateLocalVariables(-1, 0, &updateLocalVariables  );// Used to check and update Local Variables
//
//Task taskReadData(-1,TASK_FOREVER, &readData );// Used to check and update Local Variables
//
//Task taskAlgorithm(-1, 0, &algorithm );
//
//Task taskGatherData(TASK_SECOND*1 ,1000, &gatherData );
//
//Task taskobstacleAvoidance(-1, 0, &obstacleAvoidance );
//
//Task taskMovement(-1, 0, &movements );

  bool firstTime = false;


  //Global Variables
  float g_best[3];

  //Local Variables
  float l_best[3];
  float l_current[3];
  float movement[2];
  
  //Setup Arrays
  float gps[5];
  float imu_data[7];
  float lidar_sweep[100];
  float temp_sweep_min[1];

  //Parameters
  float dist_threshold = 100;





//**********************************************************************
// Primary Functions - SETUP (runs 1 time) and LOOP (runs Infinite times)
void setup() {
  Serial.begin(115200);
//  startMillis = millis();
  //mesh.setDebugMsgTypes( ERROR | MESH_STATUS | CONNECTION | SYNC | COMMUNICATION | GENERAL | MSG_TYPES | REMOTE ); // all types on
  //MESH FUNCTION
  mesh.setDebugMsgTypes( ERROR | STARTUP );  // set before init() so that you can see startup messages
  mesh.init( MESH_PREFIX, MESH_PASSWORD, &userScheduler, MESH_PORT );
  mesh.onReceive(&receivedCallback);
  mesh.onNewConnection(&newConnectionCallback);
  mesh.onChangedConnections(&changedConnectionCallback);
  mesh.onNodeTimeAdjusted(&nodeTimeAdjustedCallback);

  //GPS
//  GPS.begin(9600);
//  GPS.sendCommand(PMTK_SET_NMEA_OUTPUT_RMCGGA);  // uncomment this line to turn on RMC (recommended minimum) and GGA (fix data) including altitude
//  GPS.sendCommand(PMTK_SET_NMEA_UPDATE_1HZ); // 1 Hz update rate
  // For the parsing code to work nicely and have time to sort thru the data, and
  // print it out we don't suggest using anything higher than 1 Hz

  //MPU
  // Set registers - Always required
//  imu.setup();
  // Initial calibration of gyro
//  imu.setBias();

  //Servos
//  Wire.begin();
  
  //TASK SCHEDULER
  userScheduler.addTask( taskSendMessage );
//  userScheduler.addTask(taskGatherData);
//  taskGatherData.enable();
  taskSendMessage.enable();

//  ledcSetup(PWMChannel, PWMFreq, PWMResolution);
//  ledcAttachPin(servoPin, PWMChannel);
//  ledcWrite(PWMChannel, dutyCycle);
//  
  
}

void loop() {
  mesh.update();   // it will run the user scheduler as well
}

//____________________________________________________________________________________________________________________________________________________________________________
//**********************************************************************
//**********************************************************************
// Custom Functions - These will be divided into different categories

//**********************************************************************
// Painless Mesh Main Functions
void sendMessage() {
  String msg = "BASE_STATION:";
  msg += gatherData();
  mesh.sendBroadcast( msg );
  taskSendMessage.setInterval( random( TASK_SECOND * 1, TASK_SECOND * 5 ));
}

// Needed for painless library
void receivedCallback( uint32_t from, String &msg ) {
  Serial.printf("%u msg=%s\n", from, msg.c_str());
}

void newConnectionCallback(uint32_t nodeId) {
  Serial.printf("New Connection, nodeId = %u\n", nodeId);
}

void changedConnectionCallback() {
  Serial.printf("Changed connections\n");
}

void nodeTimeAdjustedCallback(int32_t offset) {
  Serial.printf("Adjusted time %u. Offset = %d\n", mesh.getNodeTime(), offset);
}


//**********************************************************************
// Robot Motion Main Functions

void forward(double inches) {
//  currentMillis = millis();
  while ((currentMillis - startMillis) != (timeConstInches * inches)) {
    motors.forward();
  }
  motors.stop();

}

void turn(double degree, char dir) {
//  currentMillis = millis();
  while ((currentMillis - startMillis) != (timeConstDegree * degree)) {
    if (dir == 'L') {
      motors.forwardA();
      motors.backwardB();
    } else {
      motors.backwardA();
      motors.forwardB();
    }
  }
  motors.stop();
}

void reverse(double inches) {
  currentMillis = millis();
  while ((currentMillis - startMillis) != (timeConstInches * inches)) {
    motors.backward();
  }
  motors.stop();
}

//**********************************************************************
// GPS Data Main Functions
void GPSData() {
//  currentMillis = millis();
  char c = GPS.read();    // read data from the GPS in the 'main loop'
  if (GPSECHO)
    if (c) Serial.print(c);  // if you want to debug, this is a good time to do it!
  // approximately every 2 seconds or so, print out the current stats
  if (currentMillis - startMillis > period * 2) {
    if (GPS.fix) {
      gps[0] = GPS.latitude;
      gps[1] = GPS.longitude;
      gps[2] = GPS.altitude;
      gps[3] = GPS.angle;
      gps[4] = GPS.satellites;
    }
  }
}

//**********************************************************************
// IMU Main Functions

String IMUData() {
  String temp;
  // Update gyro calibration 
//  imu.updateBias();
//  imu.setup();
  if(firstTime == false){
    imu.setup();
    imu.setBias();
    firstTime = true;
  }else{
  imu.updateBias();
//  imu_data[0]= imu.ax();
//  imu_data[1]= imu.ay();
//  imu_data[2]= imu.az();
//  imu_data[3]= imu.gx();
//  imu_data[4]= imu.gy();
//  imu_data[5]= imu.gz();
//  imu_data[6]= imu.temp();
    temp +="x: ";
    temp +=String(imu.ax(),3);
    return temp;
  }
}

//**********************************************************************
// LIDAR Main Functions

//void LIDARScanData() {
//  if ( tflI2C.getData(tfDist, tfAddr)) // If read okay...
//  {
//    Serial.print("Dist: ");
//    Serial.println(tfDist);          // print the data...
//  }
//  else tflI2C.printStatus();           // else, print error.
//}

void LiDARSweep(){
  if ( tflI2C.getData(tfDist, tfAddr)){ // If read okay...
    ledcWrite(PWMChannel, 200);                     //approx 1ms
    for(int i = 0; i<100;i++){
      lidar_sweep[i] = tfDist;
    }
  }
  else tflI2C.printStatus();           // else, print error. 
}


//**********************************************************************
// Particle Swarm Optimization Tasks

String gatherData(){
  String values = IMUData();
//  GPSData();
//  LiDARSweep();
  return values;
}

//void obstacleAvoidance(){
//  LiDARSweep();
//  float temp_sweep_min = lidar_sweep[0];
//  for(int i = 0; i<sizeof(lidar_sweep);i++){
//    if(lidar_sweep[i]<temp_sweep_min){
//      temp_sweep_min = lidar_sweep[i];
//    }
//  }
//  if(temp_sweep_min < dist_threshold){
//    reverse(2);
//    turn(45, 'R');
//    forward(2);
//  }
//
//}
//
//void randomStart(){
//  forward(random(1,5));
//  turn(random(1,90),'L');
//  forward(random(1,5));
//  taskGatherData.enableDelayed(1000);
//}
//
//void updateLocalVariables(){
//  l_current[0] = gps[0];
//  l_current[1] = gps[1];
//  l_current[2] = gps[2];
//  taskReadData.enableDelayed(1000);
//}
//
//void updateGlobalVariables(){
//}
//
//void movements(){
//  float dist = sq(pow(movement[0],2)+pow(movement[1],2));
//  char where[1];
//  
//  if(movement[0] > 0){
//    where[0] = 'L';
//  }else{
//    where[0] = 'R';
//  }
//  if(movement[1] > 0){
//    where[1] = 'D';
//  }else{
//    where[1] = 'U';
//  }
//
//
//  if(where[0] == 'L' & where[1] == 'D'){
//    turn(135,'L');
//    forward(dist);
//  }if(where[0] == 'L' & where[1] == 'U'){
//    turn(45,'L');
//    forward(dist);
//  }
//
//  if(where[0] == 'R' & where[1] == 'D'){
//    turn(135,'R');
//    forward(dist);
//  }if(where[0] == 'R' & where[1] == 'U'){
//    turn(45,'R');
//    forward(dist);
//  }
////    taskGatherData.enableDelayed(1000);
//}
//
//void algorithm(){
//  //Check if we are at better than global
//  if(l_best[0] > g_best[0] & l_best[1] > g_best[1]){
//    g_best[0] = l_best[0];
//    g_best[1] = l_best[1];
//  }
//  //Check each dimension
//  //X
//  if(l_current[0]>l_best[0]){
//    movement[0] = (l_current[0]-l_best[0]);
//  }
//  if(l_current[0]<l_best[0]){
//    movement[0] = (l_current[0]-l_best[0]);
//  }
//  //Y
//  if(l_current[1]>l_best[1]){
//    movement[1] = (l_current[1]-l_best[1]);
//  }
//  if(l_current[1]<l_best[1]){
//    movement[1] = (l_current[1]-l_best[1]);
//  }
//  taskMovement.enableDelayed(1000);
//}
//void readData(){
//  taskAlgorithm.enableDelayed(1000);
//}

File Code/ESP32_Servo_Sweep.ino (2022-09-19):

/*
On ESP32 generates a sweeping pulse of 1mS to 2mS at 50hz
*/

const int servoPin = 17;

int dutyCycle = 0;

const int PWMFreq = 50;                                //50hz
const int PWMChannel = 0;
const int PWMResolution = 12;                       //12 bits 0-4095
 
void setup()
{
  ledcSetup(PWMChannel, PWMFreq, PWMResolution);
  ledcAttachPin(servoPin, PWMChannel);
  ledcWrite(PWMChannel, dutyCycle);
}

void loop()
{
    ledcWrite(PWMChannel, 200);                     //approx 1ms
    delay(2000);

    ledcWrite(PWMChannel, 400);                     //approx 2mS
    delay(2000);
}
